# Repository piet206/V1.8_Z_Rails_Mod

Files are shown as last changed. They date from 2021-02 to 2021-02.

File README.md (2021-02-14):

# V1.8_Z_Rails_Mod
**Z Linear Rail Mod for Voron 1.8 (300x300x250)**

**Parts list:**
* 2 modified z motor mounts (printed in abs with the standard voron settings)
* 2 leadscrew-mgn12 blocks (printed in abs with the standard voron settings)
* 2 mgn12h (300mm long for 250 z) 
* 4 m3x16 shcs (fasten lead screw nut to block)
* 4 m3 nuts (fasten lead screw nut to block)
* 12 m5x16 bhcs (fasten blocks to extrusions and extrusions to frame)
* 8 m5 t-nuts 
* 8 m3x20 shcs (fasten blocks to mgn12's)
* 2 Misumi HFS5-2020-340-TPW (vertical extrusions for 250 z height)
* 12 m3x8 shcs (fasten mgn12 to extrusion)
* 12 m3 t-nuts
* 2 Misumi HFS5-2020-350-AH10-BH340 (x extrusions for 300x300 bed frame)

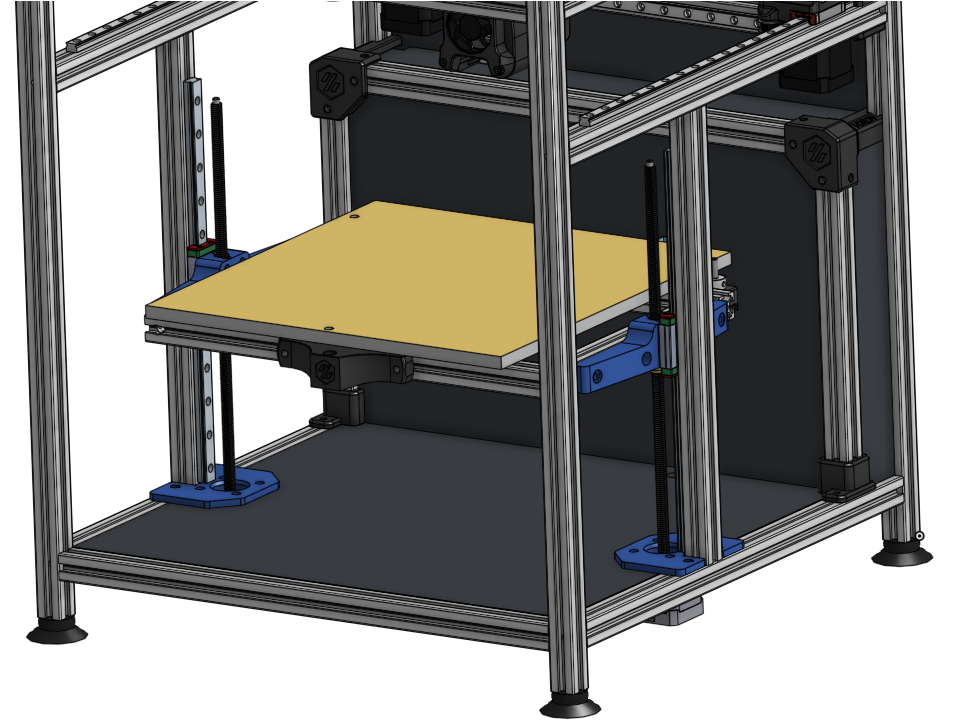
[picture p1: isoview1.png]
isoview1


**Notes:**

The z motors are shifted inwards 2.07 mm (towards the center of the bed) so you must modify the deck panel slighly. This was necessary to provide clearance for the rails. See the dxf folder for the modified dimensions.

The y extrusions have an allen key clearance hole drilled 170.8 mm from the front end cut (145.8 mm for 250 build). This is for the blind joint that fastens the new extrusions the mgn12's are mounted to. These 2 extrusions are in line with center of the bed. It is very important that the end cuts are square and exactly the same length. This can potential bend your gantry extrusions if they are not square. I did not have any issues with Misumi's end cuts. Others have used right angle brackets with success and this might be a better way.

I've added leadscrew-mgn12 block stl's for both the 300 and 250 build sizes so choose accordingly.
I had trouble with warping when printing the leadscrew-mgn12 blocks on my ender 3 with a glass bed. Elmers purple gluestick on the buildplate saved the day.
These blocks have been tested with the link cnc 8x2 and bigtreetech 8x8 integrated lead screws. I highly recommend the [bigtreetech](https://www.aliexpress.com/item/32977907686.html?spm=a2g0s.9042311.0.0.43bf4c4drPPHbq) 8x8 lead screws with the only downside being that the bed drops slighly when the motors turn off. 

You can center the mgn12 to 2020 extrusions using the stl located in the switchwire repo [here](https://github.com/VoronDesign/Voron-Switchwire/blob/master/STL/Gantry/2020_MGN12_guide_x2.stl).

The 2 bed extrusions in the x direction are shortened to 350mm because they're no longer necessary to hold the lm8luu bearing mounts. Although the stock length extrusions (420mm) will still work, they will be protruding out in space.

Let me know if you have any questions or need anything. There is also a video of my mod on [youtube](https://www.youtube.com/watch?v=qd7ciNlM-1k) if you would like to see it in action.

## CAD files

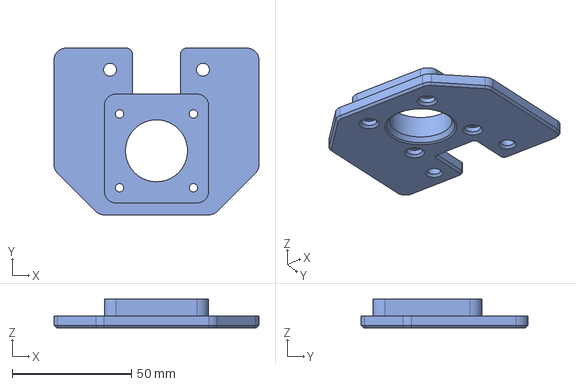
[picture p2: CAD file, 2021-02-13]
cad/ZMotorMount.step
86.0 x 70.0 x 12.0 mm

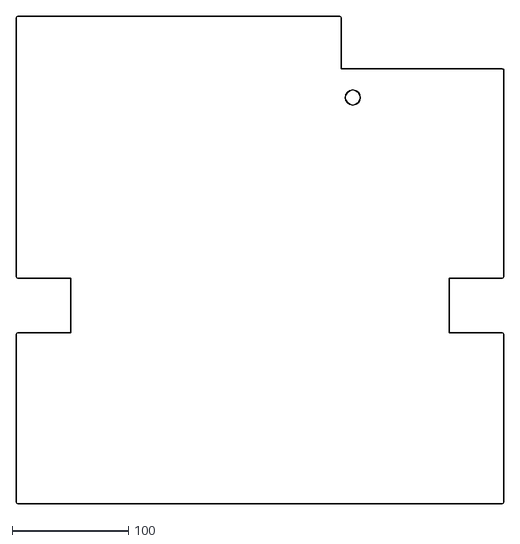
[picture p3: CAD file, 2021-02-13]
dxf/Deck Panel Revised.dxf
420.0 x 420.0

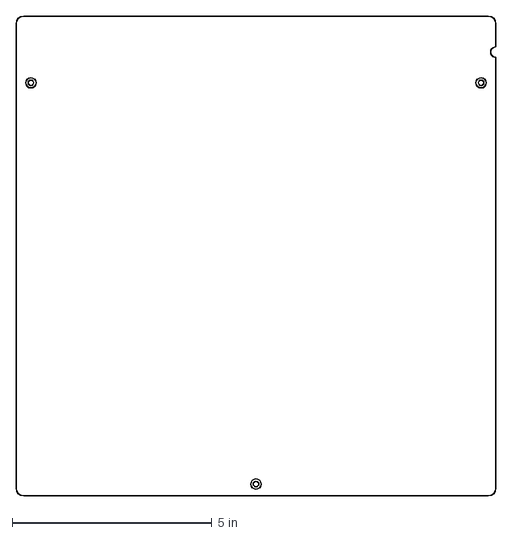
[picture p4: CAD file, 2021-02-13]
dxf/PartBed1.dxf
12.0 x 12.0 in

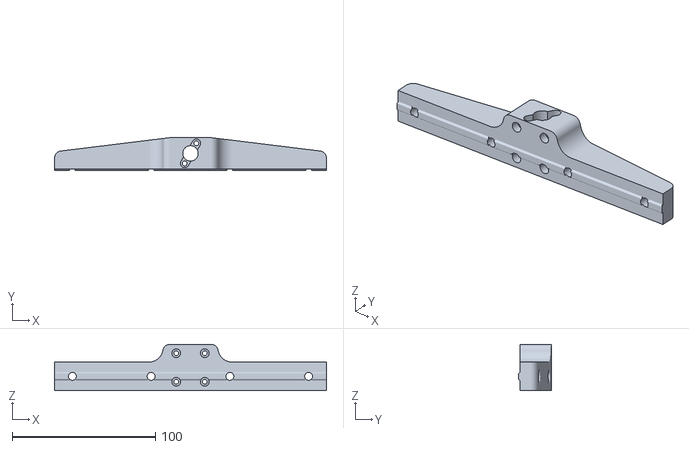
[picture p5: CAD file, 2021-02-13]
stl/300LeadScrewBlock.stl
190.0 x 22.9 x 32.4

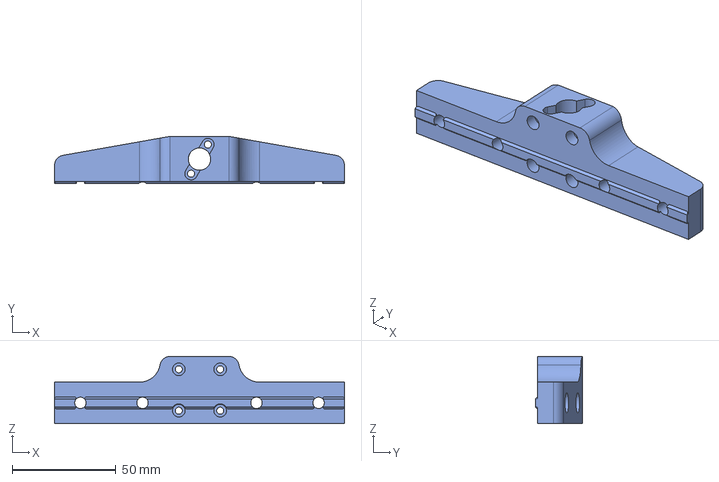
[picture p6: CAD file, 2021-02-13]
cad/250LeadScrewBlock.step
140.0 x 22.9 x 32.4 mm

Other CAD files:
cad/300LeadScrewMount.step
stl/250LeadScrewBlock.stl
stl/ZMotorMount.stl
